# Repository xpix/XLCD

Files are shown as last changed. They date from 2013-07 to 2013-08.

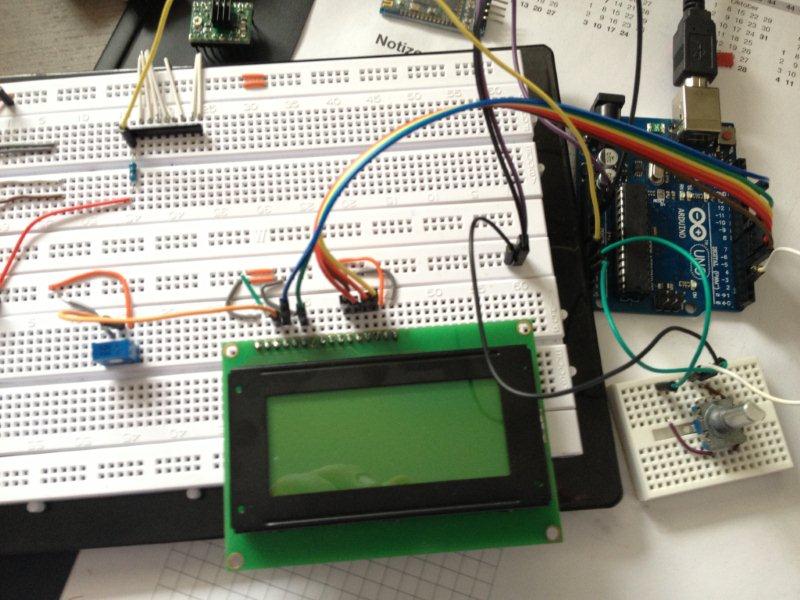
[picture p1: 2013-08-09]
BuildLog/Breadboard.jpg

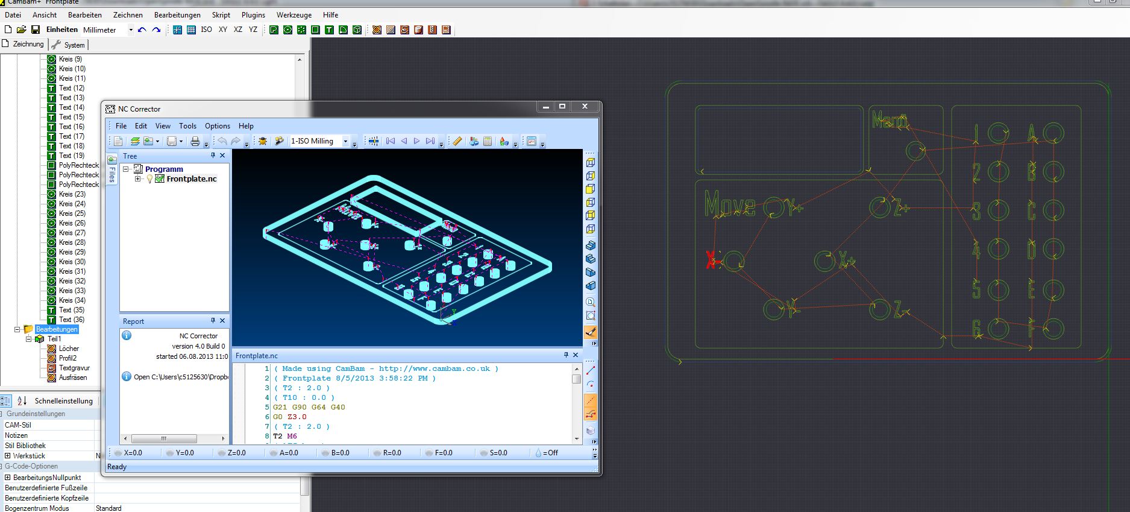
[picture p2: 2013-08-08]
eagleUp/FrontplateDesign_01.JPG

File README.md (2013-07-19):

XStepperLCD
===========

LCD Module for XStepper

Some time ago, we designed and built version 1.0 of Xstepper.  Unlike other existing GRBL-based CNC solutions, Xstepper is an all-in-one device.  The possibility of controlling the machine in a headless state may be possible, and the first step toward doing so is some sort of visual display.  This module aims at solving part of the problem!

But how?  The good people coding GRBL don’t have the on-chip memory to code in an LCD interface for GRBL.  Add to that the severe lack of available IO and this seems to rule out this type of expansion.  However, there is always a workaround.

This module spies on the serial communication between the arduino and PC using an ATtiny85.  Simultaneously the ATtimy polls the position of the spindle from the XStepper.  The returned data is then parsed and displayed on a local LCD.  You can choose to display the debug screen, work position or machine position using the on-board button.

sketchup preview

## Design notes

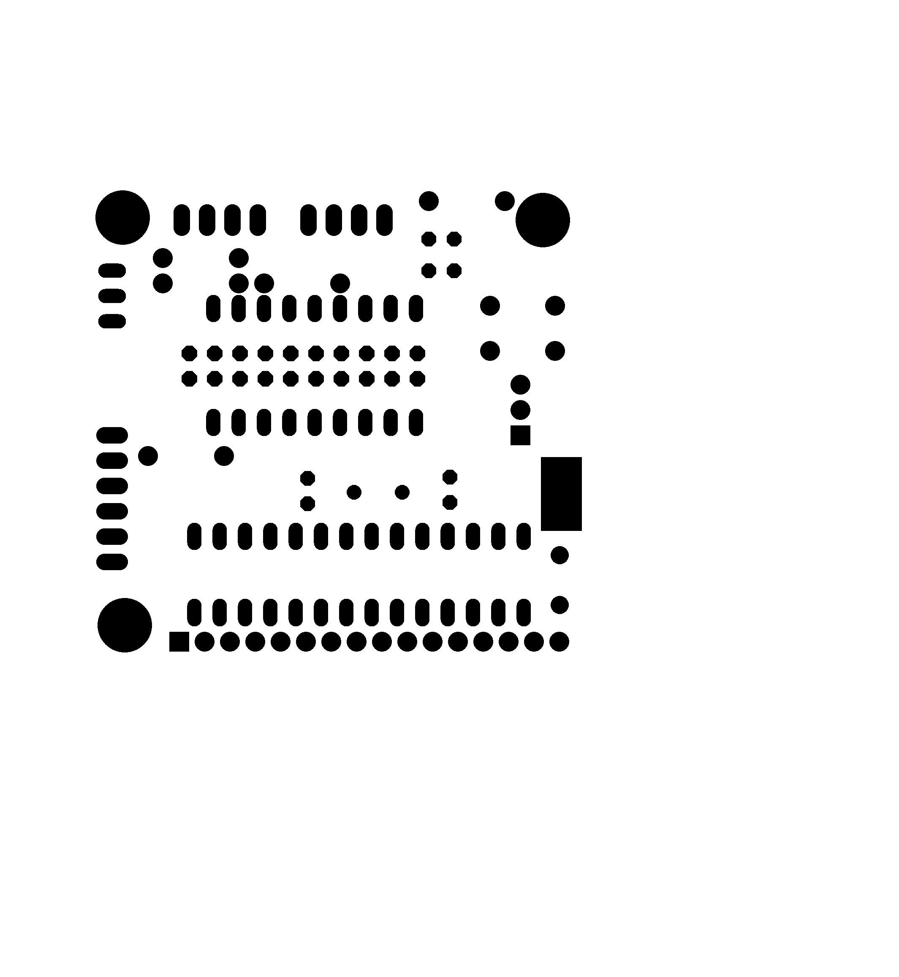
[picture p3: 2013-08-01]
eagleUp/eagleUp_XStepperLCD_bottom_mask.png

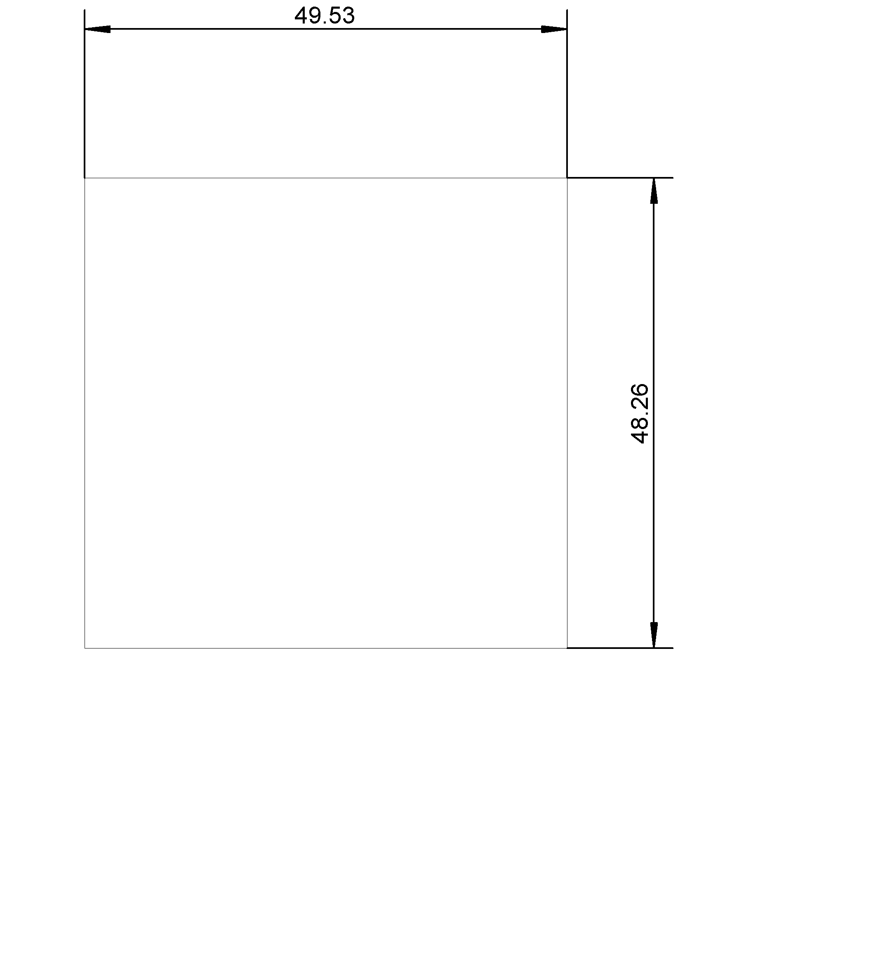
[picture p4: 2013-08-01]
eagleUp/eagleUp_XStepperLCD_outline.png

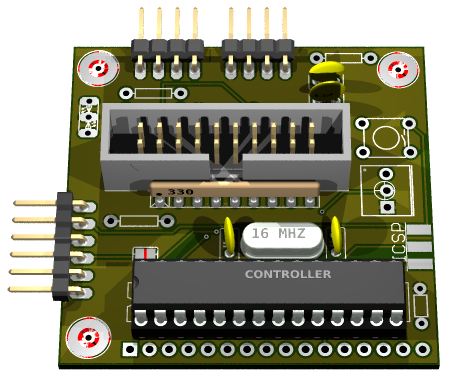
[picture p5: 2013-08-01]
eagleUp/sketchup.JPG

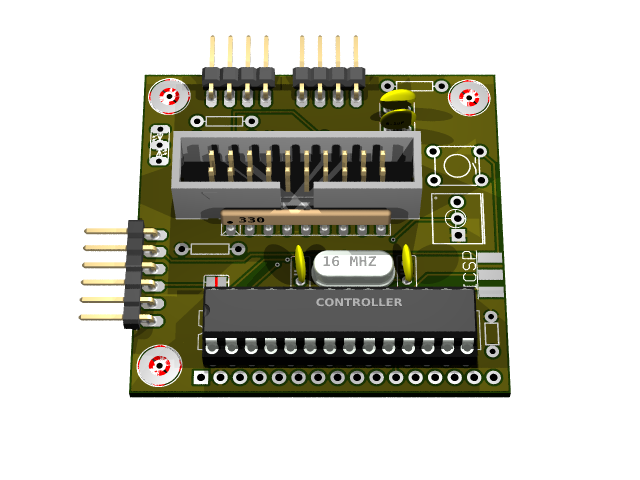
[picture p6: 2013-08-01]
eagleUp/XStepperLCD.bmp

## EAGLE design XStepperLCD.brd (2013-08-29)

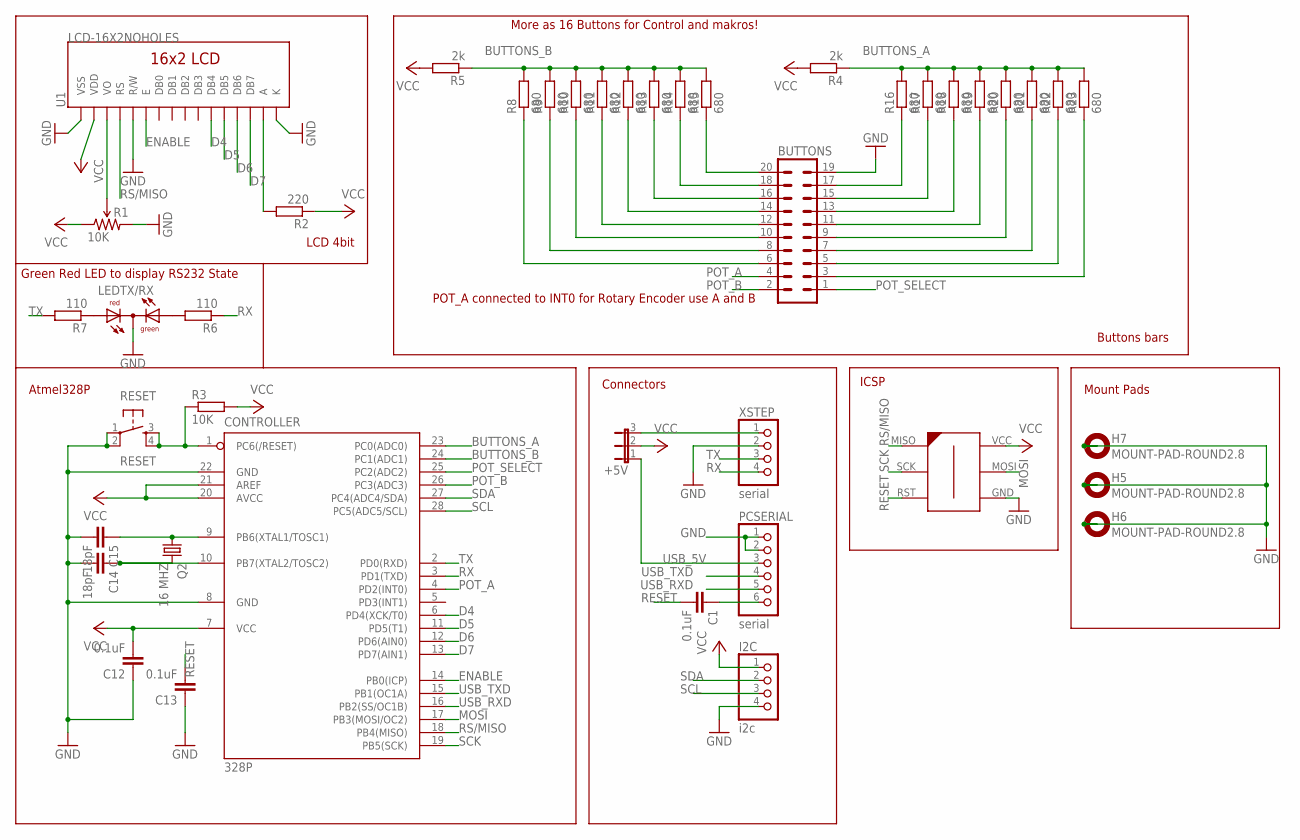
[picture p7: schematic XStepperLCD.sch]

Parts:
328P: CONTROLLER; DIL28-3
+5V: JP2E; JP2
BUTTONS: ML20
C1, C13: 0.1uF; C1206
C12: 0.1uF; C1206K
C14, C15: 18pF; C025-025X050
H5, H6, H7: MOUNT-PAD-ROUND2.8; 2,8-PAD
I2C: i2c; 1X04/90
ICSP: ICSP; 6PAD_ISP
LEDTX/RX: DUOLED2X5
PCSERIAL: serial; 1X06/90
Q2: 16 MHZ; HC49/S
R1: 10K; 3362U-2
R2: 220; R1206
R3: 10K; R1206
R4, R5: 2k; R1206
R6, R7: 110; R1206
R8, R9, R10, R11, R12, R13, R14, R15, R16, R17, R18, R19, R20, R21, R22, R23: 680; R1206
RESET: RESET; TACTILE-PTH
U1: LCD-16X2NOHOLES; LCD-16X2_NOHOLES
XSTEP: serial; 1X04/90

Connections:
BUTTONS_A: 328P.23 (PC0(ADC0)), R4.1, R16.2, R17.2, R18.2, R19.2, R20.2, R21.2, R22.2, R23.2
BUTTONS_B: 328P.24 (PC1(ADC1)), R5.1, R8.2, R9.2, R10.2, R11.2, R12.2, R13.2, R14.2, R15.2
D4: 328P.6 (PD4(XCK/T0)), U1.11 (DB4)
D5: 328P.11 (PD5(T1)), U1.12 (DB5)
D6: 328P.12 (PD6(AIN0)), U1.13 (DB6)
D7: 328P.13 (PD7(AIN1)), U1.14 (DB7)
ENABLE: 328P.14 (PB0(ICP)), U1.6 (E)
GND: 328P.8 (GND), 328P.22 (GND), BUTTONS.19, C12.1, C13.1, C14.2, C15.2, H5.B2,8, H6.B2,8, H7.B2,8, I2C.4, ICSP.GND, LEDTX/RX.K (C), PCSERIAL.1, PCSERIAL.2, R1.3 (CW), RESET.1, RESET.2, U1.1 (VSS), U1.5 (R/W), U1.16 (K), XSTEP.2
MOSI: 328P.17 (PB3(MOSI/OC2)), ICSP.MOSI
unnamed: R1.2 (WIPER), U1.3 (VO)
unnamed: R2.2, U1.15 (A)
unnamed: BUTTONS.13, R18.1
unnamed: BUTTONS.15, R17.1
unnamed: BUTTONS.17, R16.1
unnamed: BUTTONS.6, R8.1
unnamed: BUTTONS.8, R9.1
unnamed: BUTTONS.3, R23.1
unnamed: BUTTONS.5, R22.1
unnamed: BUTTONS.10, R10.1
unnamed: BUTTONS.12, R11.1
unnamed: BUTTONS.14, R12.1
unnamed: C1.1, PCSERIAL.6
unnamed: BUTTONS.16, R13.1
unnamed: BUTTONS.7, R21.1
unnamed: BUTTONS.9, R20.1
unnamed: BUTTONS.11, R19.1
unnamed: BUTTONS.18, R14.1
unnamed: BUTTONS.20, R15.1
unnamed: LEDTX/RX.AG, R6.2
unnamed: LEDTX/RX.AR, R7.1
unnamed: 328P.9 (PB6(XTAL1/TOSC1)), C15.1, Q2.1
unnamed: 328P.10 (PB7(XTAL2/TOSC2)), C14.1, Q2.2
POT_A: 328P.4 (PD2(INT0)), BUTTONS.4
POT_B: 328P.26 (PC3(ADC3)), BUTTONS.2
POT_SELECT: 328P.25 (PC2(ADC2)), BUTTONS.1
RESET: 328P.1 (PC6(/RESET)), C1.2, C13.2, ICSP.RST, R3.1, RESET.3, RESET.4
RS/MISO: 328P.18 (PB4(MISO)), ICSP.MISO, U1.4 (RS)
RX: 328P.3 (PD1(TXD)), R6.1, XSTEP.4
SCK: 328P.19 (PB5(SCK)), ICSP.SCK
SCL: 328P.28 (PC5(ADC5/SCL)), I2C.3
SDA: 328P.27 (PC4(ADC4/SDA)), I2C.2
TX: 328P.2 (PD0(RXD)), R7.2, XSTEP.3
USB_5V: +5V.1, PCSERIAL.3
USB_RXD: 328P.16 (PB2(SS/OC1B)), PCSERIAL.5
USB_TXD: 328P.15 (PB1(OC1A)), PCSERIAL.4
VCC: 328P.7 (VCC), 328P.20 (AVCC), 328P.21 (AREF), +5V.2, C12.2, I2C.1, ICSP.VCC, R1.1 (CCW), R2.1, R3.2, R4.2, R5.2, U1.2 (VDD)
XSTEP_5V: +5V.3, XSTEP.1

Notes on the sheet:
Connectors
ICSP
Atmel328P
Mount Pads
Buttons bars
Green Red LED to display RS232 State
LCD 4bit
POT_A connected to INT0 for Rotary Encoder use A and B
More as 16 Buttons for Control and makros!

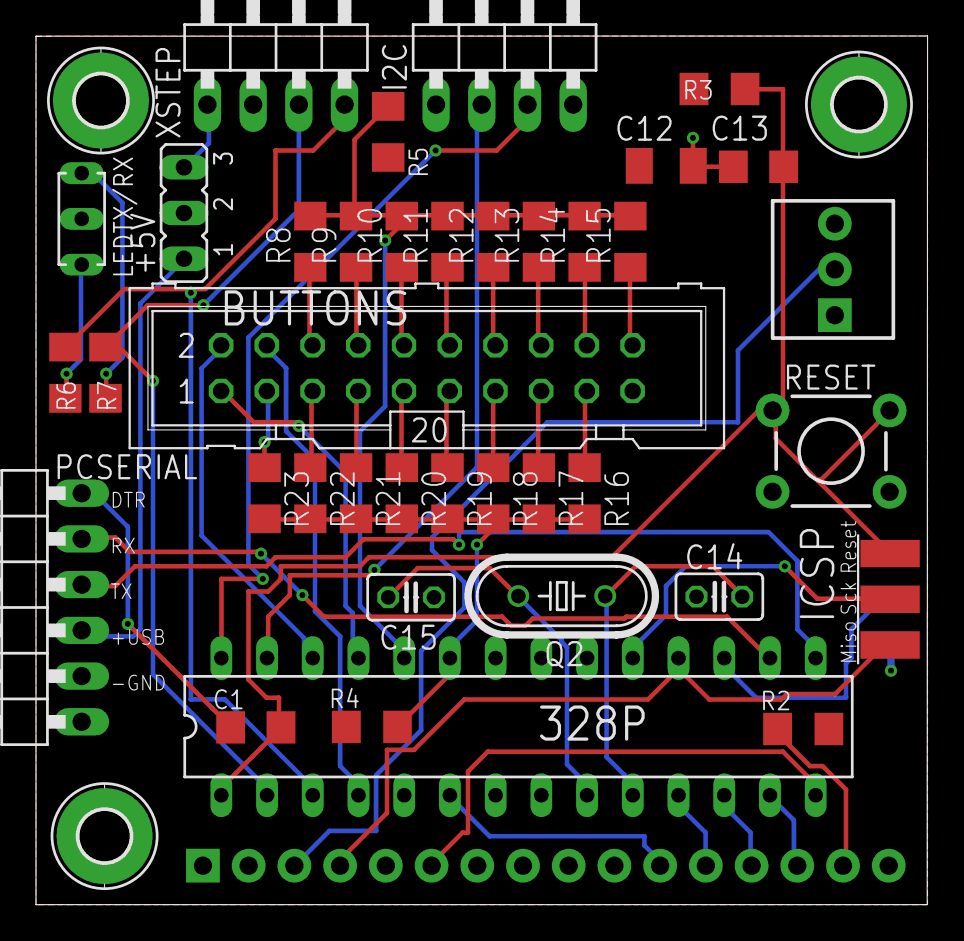
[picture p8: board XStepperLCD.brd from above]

Board: 2 copper layers, 49.5 x 48.3 mm, 42 parts (0 on the bottom side), 47 nets.

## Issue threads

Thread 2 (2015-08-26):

Information request

ArcAIN6, 2015-08-26:
Since i don't have an XStepper, is there a way to use this using an arduino Uno with GRBL on it, and an Arduino Mega?

I.e. PC <=> Mega[LCD, Keypad, menu system etc] <=> Uno[GRBL]

xpix, 2015-08-27:
Sure, xlcd are only a proxy between PC and GRBL. XLCD get data from PC and send this 1:1 to GRBL.

ArcAIN6, 2015-08-27:
So i can just load this onto the mega? Or do i need to build the LCD module shown on the front page, and load XLCD onto that?

xpix, 2015-08-27:
Try an UNO or other Arduino first and please use version 0.3 https://github.com/xpix/XLCD/tree/xlcd-0.3. For an mega you have change the pins for serial ports.

ArcAIN6, 2015-08-27:
will give it a shot now :) So happy this exists.

ArcAIN6, 2015-08-27:
hrm. I seem to have run into an error on verifying. Getting error on line 14 of lcd_screens.

Is there an error with the actual code, or am i using outdated libraries (Using the libraries supplied  by the wiki.)

lcd_screens:14: error: #elif with no expression
commands.ino: In function 'void learn_button()':
commands:46: error: 'BUTTONS_A_ADC_PIN' was not declared in this scope
commands:48: error: 'BUTTONS_B_ADC_PIN' was not declared in this scope
commands.ino: In function 'void press_button(String)':
commands:61: error: 'getValue' was not declared in this scope
commands.ino: In function 'void setinterval(String)':
commands:75: error: 'getValue' was not declared in this scope
commands.ino: In function 'void memoryfree()':
commands:94: error: 'freeMemory' was not declared in this scope
console.ino: In function 'void resetDevice(int)':
console:146: error: redefinition of 'void resetDevice(int)'
commands:86: error: 'void resetDevice(int)' previously defined here
#elif with no expression

xpix, 2015-08-28:
I have no idea :) i realize this 2 years ago!
But maybe i can send you an Arduino IDE that works with it. Please check also the forum in shapeoko, some peoples try to make it better http://www.shapeoko.com/forum/viewtopic.php?f=11&t=1904&p=50530&hilit=XLCD#p50530

My Advice, remove all button and unused functions and try to make it only with LCD and Serial sniffing :)

xpix, 2015-08-28:
Please try to compile this fork:

https://github.com/soundstorm/XLCD

ArcAIN6, 2015-08-28:
wierd... it seems to verify with arduino IDE 1.5.4, but not the latest..

however, i think there's going to be a lot of tinkering on my end, as the LCD i have is an LCD keypad shield with 5 buttons + reset, and there is no RW pin.
I'll see if i can figure out a workaround..

    Pin 4 (DB4)
    Pin 5 (DB5)
    Pin 6 (DB6)
    Pin 7 (DB7)
    Pin 8 (RS)
    Pin 9 (Enable)
    Pin 10 (Backlight)
    Analog 0 - Push button switches

ArcAIN6, 2015-08-28:
well.. i couldn't really figure out how to get it to work. So i started all over and have been writing something based upon my own hardware.. It is way less complex than yours of coarse, and there aren't a lot of features. But if you are interested, i have uploaded it to one of my domains, and maybe you can take a look at it, give some advice or pointers where i can easily add features, or simplify things.

http://www.thegamerzhost.com/LCDKeypadMenuTemplate2.rar

Closed 2015-08-28.

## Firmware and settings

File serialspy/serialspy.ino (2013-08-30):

/* ===============================================
 * Project: XLCD
 * ===============================================
 * Autor:     Frank (xpix) Herrmann
 * Email:     xpixer@gmail.com
 * License:   all Free
 * Last edit: 30.08.2013
 */ 

/* 
 * ===============================================
 * Includes
 * =============================================== 
 */
#include <simpleThread.h>
#include <AltSoftSerial.h>
//#include <SoftwareSerial.h>
#include <MemoryFree.h>
#include <EEPROMEx.h>
#include <phi_interfaces.h>

// local libs
#include "LCDMenu.h"


/* Prototype on Arduino UNO or compatible
 * Frank (xpix) Herrmann / 07/2013
 *
 */

/* 
 * ===============================================
 * Defines
 * =============================================== 
 */

// Makros
#define COUNT_OF(x) ((sizeof(x)/sizeof(0[x])) / ((size_t)(!(sizeof(x) % sizeof(0[x])))))

// XXX: 
// Test with SoftwareSerial, because AltSerial need Ports 8 and 9. 
// PCB Design use follow Connects
//    PC => ( Soft: 9,10 ) => XLCD => (UART: 0,1) => XStepper

// GRBL Serial connect pins
// SoftwareSerial (NewSoftSerial)
#define GRBL_RX     9
#define GRBL_TX     10 
// AltSoftSerial
//#define GRBL_RX        8
//#define GRBL_TX        9 

// LCD
//#define LCD_ADDR        0x27  // I2C LCD Address
#define LCD_4BIT
#define LCD_cols                          16
#define LCD_rows                          4

// Rotary Encoder
#define ENC_A           2   // Encoder interrupt pin
#define ENC_B           A3  // Encoder second pin
#define ENC_S           A2  // Encoder select pin

// Buttons
#define BUTTONS_A_ADC_PIN  A0    // A0 is the button ADC input A
#define BUTTONS_B_ADC_PIN  A1    // A1 is the button ADC input B

// Measure Power on when pressed button and note this value here
// use resistor network 680 Ohm
// Buttons:            0   1   2    3    4    5    6    7
int button_power[] = {30, 262, 415, 517, 589, 643, 685, 718}; // Power data for every pressed button

String			LINE;
String			CMDLINE;
char				GRBL_FIRST_CHAR;
char				PC_FIRST_CHAR;
volatile char	rotary_key;   // flag, follow button press
volatile byte  button_pressed;
boolean        proxymode = true;


/* 
 * ===============================================
 * Inits
 * =============================================== 
 */
AltSoftSerial grblSerial;
//SoftwareSerial grblSerial(GRBL_RX, GRBL_TX); // RX, TX

// Add Threads to refresh status informations from GRBL
#define _sT_cnt  _sT_cnt_2    // count of threads(?, $G)
simpleThread_init(_sT_cnt);   // init threads

// Describe threads
simpleThread_new_timebased_dynamic  (_sT_P1  , _sT_millis,  500, _sT_start , getPositions);	// get position info (?)
simpleThread_new_timebased_dynamic  (_sT_P2  , _sT_millis, 2000, _sT_start , getStates);	// get state info ($G) (not supported from UniversalGcodeSender)


// Rotary Encoder
#if defined(ENC_A)
	// Rotary Encoder
	char mapping1[]={'R','L'}; // This is a rotary encoder so it returns U for up and D for down on the dial.
	phi_rotary_encoders myEncoder(mapping1, ENC_A, ENC_B, 12);

	char mapping[]={'S'}; // This is a list of names for each button.
	byte pins[]={ENC_S}; // The digital pins connected to the 6 buttons.
	phi_button_groups myEncoderButton(mapping, pins, 1);
#endif

// Analog Buttons
#if defined(BUTTONS_A_ADC_PIN)
	byte keypad_type=Analog_keypad;
	char key_mapping_analog_a[]={'1','2','3','4','5','6','7'}; // This is an analog keypad A.
	byte pins_a[]={BUTTONS_A_ADC_PIN};
	phi_analog_keypads pad_a(key_mapping_analog_a, pins_a, button_power, 1, 7);

	char key_mapping_analog_b[]={'A','B','C','D','E','F','G'}; // This is an analog keypad B.
	byte pins_b[]={BUTTONS_B_ADC_PIN};
	phi_analog_keypads pad_b(key_mapping_analog_b, pins_b, button_power, 1, 7);
#endif

// All inits for LCD control
#if defined(LCD_4BIT)
   #include <LiquidCrystalFast.h>   // LCD
   LiquidCrystalFast myLCD(12, 11, 4, 5, 6, 7);
#elif defined(LCD_ADDR)
   #include <Wire.h>                // I2C Communication
   #include <LiquidCrystal_I2C.h>   // LCD over I2C
   // Set the pins on the I2C chip used for LCD connections:
   //                         addr, en,rw,rs,d4,d5,d6,d7,bl,blpol
   LiquidCrystal_I2C myLCD(LCD_ADDR, 2, 1, 0, 4, 5, 6, 7, 3, POSITIVE);  // Set the LCD I2C address
#endif

// LCD Menu
// look in lcd_menu.ino for build menus
LCDMenu menu(&myLCD, LCD_cols, LCD_rows);





/* 
 * ===============================================
 * Main
 * =============================================== 
 */

/*  ---------- Setup  ----------- */

void setup() 
{ 
   /* init threads */
   simpleThread_initSetup(_sT_cnt);

   myLCD.begin(16,4); // letter, row

   myLCD.setCursor(0,0); // letter, row
   myLCD.print(F("XLCD 0.1"));
   myLCD.setCursor(0,1); // letter, row
   myLCD.print(F("Connect ... "));

	menu_root(0); // init root menu but don't display

   // This is the serial connect to PC, we get some commands
   // but we can also print some additional information about this module
   // and the parser from Client program will ignore this  
   Serial.begin(9600);   // open serial to PC
   Serial.println(F("<XLCD 0.1>"));
   Serial.println(F("<All commands for XLCD start with a colon ':'>"));
   Serial.println(F("<Call help with ':?'>"));
  
   delay(1000);

   // open serial port to GRBL
   grblSerial.begin(9600); // open serial to grbl
   // reset grbl device (ctrl-X) for Universal Gcode Sender
   grblSerial.write(0x18);

   myLCD.clear();
}//SETUP



/*  ---------- Loop ----------- */
void loop() 
{ 
   // Jobs
	simpleThread_run(_sT_priority);

   // Read key from Rotary Encoder
	rotary_key = myEncoder.getKey();
	if(rotary_key == NO_KEY){
		rotary_key = myEncoderButton.getKey();
	}
	switch(rotary_key){
		case 'R':
			menu.up();
		break;
		case 'L':
			menu.down();
		break;
		case 'S':
			menu.mselect();
	}

   // try to read a button
	button_pressed=pad_a.getKey(); // Use phi_keypads object to access the keypad
	if (button_pressed == NO_KEY){
		button_pressed = pad_b.getKey(); // Use phi_keypads object to access the keypad
	}
	if(button_pressed != NO_KEY)
		call_button(button_pressed);
   

  // Get data from GRBL ==> PC
  if (grblSerial.available()) {
    char c = grblSerial.read();

    // save first char in a line
    if(LINE.length() == 0)
      GRBL_FIRST_CHAR = c;

    // dont send all line start with a '['
    // (UniversalGcodeSender dont like it)
    if(PC_FIRST_CHAR != '[')
      Serial.print(c);

    // wait for a complete line 
    // and parse it
    if(c == '\n'){
      parseGrblLine(LINE);
      LINE = "";
    } else {
      LINE.concat(c);
    }
  }

  // Get data from PC ==> GRBL
  if (Serial.available()) {
    char c = Serial.read();

    // save first char in a line
    if(CMDLINE.length() == 0)
      PC_FIRST_CHAR = c;

    // dont send all line start with a colon(XLCD Commands)
    if(PC_FIRST_CHAR != ':')
      grblSerial.print(c);

    // wait for a complete line
    // and parse it
    if(c == '\n'){
      parsePCCommand(CMDLINE);
      CMDLINE = "";
    } else {
      CMDLINE.concat(c);
    }
  }
}//LOOP


// ---------- Subroutines -----------

// String subtext = getValue(line, ',', 2);
// Split for strings, i.e. split at command an get the third value
String getValue(String data, char separator, int index)
{
  int found = 0;
  int strIndex[] = {0, -1};
  int maxIndex = data.length()-1;

  for(int i=0; i<=maxIndex && found<=index; i++){
    if(data.charAt(i)==separator || i==maxIndex){
        found++;
        strIndex[0] = strIndex[1]+1;
        strIndex[1] = (i == maxIndex) ? i+1 : i;
    }
  }

  return found>index ? data.substring(strIndex[0], strIndex[1]) : "";
}

// Analyze every command (from PC => Xlcd) and choose an action
void parsePCCommand(String line){
  line.replace("\r","");

  // All commands with an ':' at start can control XLCD 
  if( line.indexOf(':') == 0 )  parse_command_line(line);
}

// Analyze every line and choose an action
void parseGrblLine(String line){
  line.replace("\r","");

  if( line.indexOf('<') == 0 )  parse_status_line(line);
  if( line.indexOf('[') == 0 )  parse_state_line(line);
}

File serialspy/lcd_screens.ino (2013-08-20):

/* ===============================================
 * Project: XLCD, LCD Screens
 * ===============================================
 * Autor:     Frank (xpix) Herrmann
 * Email:     xpixer@gmail.com
 * License:   all Free
 * Last edit: 30.08.2013
 */ 

unsigned long last_status = 0;

void parse_status_line(String line)
{
   // <Idle,MPos:5.529,0.560,7.000,WPos:1.529,-5.440,-0.000>

   // analyze last call time and ignore this event if last time smaller as interval
   if(millis() - last_status < simpleThread_dynamic_getLoopTime(getPositions)) 
      return;

   last_status = millis();

   // State ..
   String state = getValue(getValue(line, ',', 0), '<', 1);

   // Machine position ...
   String machinepos_x = getValue(getValue(line, ',', 1), ':', 1);
   String machinepos_y = getValue(line, ',', 2);
   String machinepos_z = getValue(line, ',', 3);

   // Working position ...
   String workingpos_x = getValue(getValue(line, ',', 4), ':', 1);
   String workingpos_y = getValue(line, ',', 5);
   String workingpos_z = getValue(getValue(line, ',', 6), '>', 0);

   // return if not state
   if(workingpos_z.length() == 0){
      return;
   }

   // Display on LCD ...
   // lcd screen
   // |--------------|
   // State  Z:555.529
   // 000.000  000.000

   // XXX: to use a switch to display work position or other things :)
   // myLCD.clear();
   // Display State and Machine position in first 2 rows
   myLCD.setCursor(0,0); // letter, row
   myLCD.print(state + "            ");
   myLCD.setCursor((LCD_cols-machinepos_z.length()),0);
   myLCD.print(machinepos_z);

   myLCD.setCursor(0,1);
   myLCD.print(machinepos_x);
   myLCD.setCursor((LCD_cols-machinepos_y.length()),1);
   myLCD.print(machinepos_y);
}

// send every second the command $G
void parse_state_line(String myBuffer)
{
   // parse myBuffer
   myBuffer.replace("[","");
   myBuffer.replace("]","");
   //             mm                   TNr Feed
   // [G0 G54 G17 G21 G90 G94 M0 M5 M9 T0 F500.000]
   String move = getValue(myBuffer, ' ', 0);
   if(move == "G")  move = "RAP";
   if(move == "G0") move = "RAP";
   if(move == "G1") move = "LIN";
   if(move == "G2") move = "CW ";
   if(move == "G3") move = "CCW";

   String plane = getValue(myBuffer, ' ', 2);
   if(plane == "G17") plane = "XY";
   if(plane == "G18") plane = "ZX";
   if(plane == "G19") plane = "YZ";

   String feedrate = getValue(myBuffer, ' ', 10);
   feedrate.replace(".000","");

   String toolnr = getValue(myBuffer, ' ', 9);
   String spindle = (getValue(myBuffer, ' ', 7) == "M5" ? "1" : "0");

   String mode = (getValue(myBuffer, ' ', 3) == "G21" ? "MM" : "IN");
   String flow = getValue(myBuffer, ' ', 6);

   // Display on LCD ...
   // |--------------|
   // S1 T1 F1000
   // MM LIN XY M1

   // Spindle
   myLCD.setCursor(0,2); //third row
   myLCD.print("S" + spindle);

   // Tool
   myLCD.setCursor(3,2);
   myLCD.print(toolnr);

   // Feed
   myLCD.setCursor(6,2); //third row
   myLCD.print(feedrate);


   // last row

   // mm or inch
   myLCD.setCursor(0,3);
   myLCD.print(mode);

   // Move mode
   myLCD.setCursor(3,3);
   myLCD.print(move);

   // Plane
   myLCD.setCursor(7,3);
   myLCD.print(plane);

   // Flow
   myLCD.setCursor(10,3);
   myLCD.print(flow);

}

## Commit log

2013-07-17 first version
    - add first board and schema design
    - add first code for atiny85
    [XStepperLCD.brd, XStepperLCD.sch]
2013-07-19 Change from attiny to uno
    Change all from tiny to uno, cuz problems memory lwak or to small. First
    alpha testversion run :)
    [serialspy.ino]
2013-07-19 Correct README from Matt
    [serialspy.ino]
2013-07-23 add config for my I2C LCD
2013-07-26 First konzept for XLCD with 328p
    [XStepperLCD.brd, XStepperLCD.sch]
2013-07-30 add conn header for buttons
    [XStepperLCD.brd, XStepperLCD.sch]
2013-08-01 pov, duo led, sketchup
    - add duo led
    - add icsp header
    - create povray file
    [XStepperLCD.brd, XStepperLCD.sch]
2013-08-02 - add 2 connects for potentiometers
    [XStepperLCD.brd, XStepperLCD.sch]
2013-08-08 - published to ITEAD order number 100015612
    - official Version XLCD 0.1
    - add some text
    - 3 pin header
    - changes from Matt
    - GND Polygon fix
    [XStepperLCD.GBL, XStepperLCD.GBO, XStepperLCD.GBP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]
2013-08-12 - use AltSoftSerial
    - first running version as SerialProxy
    - 2 tests with big gcode file send to Xstepper and display Data on LCD
    - remove Timer solution and test every line
2013-08-15 - software: add serial menu
    - add commands only for Xlcd with started colon
    - add threads to send every x seconds commands to grbl
    - split functions in separate files
2013-08-16 - add button thread
    - add output for UGS to ignore this
    - add command setinterval
    - add command memoryfree
    - add old buttons
    - use liquidfast
    - add read_buttons
    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
2013-08-19 - add button_config file for users
    - change voltage array for 680 ohm network
    - stop all thread to test buttons
    - change some textmessages
    - fix button analyse
    [config_buttons.ino, serialspy.ino]
2013-08-20 - rename all mySerial to grblSerial
    - add and use phi_interfaces for rotary encoder
    - change intervall to 500ms and 1000ms for threads
    - send reset if connected to grbl for UniversalGcodeSender
    - add call_button
    [XStepperLCD.brd, XStepperLCD.sch]
2013-08-29 - damn, misstake with branches work on master
    - add a lot changes for LCDMenu
    - use phi_interfaces for analog buttons
    - remove a lot unused code
    [XStepperLCD.brd, XStepperLCD.sch]
2013-08-30 - switch back to altsoftserial

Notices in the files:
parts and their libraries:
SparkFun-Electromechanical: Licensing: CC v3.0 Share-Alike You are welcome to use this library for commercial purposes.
